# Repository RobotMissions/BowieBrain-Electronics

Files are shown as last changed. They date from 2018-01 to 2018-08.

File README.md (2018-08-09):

# Bowie Brain Board v1.1

Robot Missions logo, a green leaf on a white diamond situated within a purple circle

Bowie Brain Board is the electronics for the [Robot Missions](http://robotmissions.org) introductory robot platform, _Bowie_.

### More information about our robot platform at the [Robot Missions Website ➞](http://robotmissions.org)

The Robot Missions Bowie Brain Board has ports for 6 servos, connections for 4 DC motors (2 controlled independently), can measure the current draw from the servos or DC motors, and has several connections for extendable modules. Microcontroller uses a [Teensy 3.6](https://www.pjrc.com/store/teensy36.html) for full functionality including data logging, or a [Teensy 3.2](https://www.pjrc.com/store/teensy32.html).

Firmware can be found here: [Bowie Library](https://github.com/RobotMissions/BowieLib) and [Bowie Shoreline](https://github.com/RobotMissions/BowieShoreline).

This board was designed in gEDA. You can edit it in [pcb-rnd](http://repo.hu/projects/pcb-rnd/).

## Pinouts

There are several ways you can extend the functionality of your Bowie robot. Here are the labeled connector ports with the according pins.

> **Note:** TX_n_ denotes data out from the brain's microcontroller, and RX_n_ is data in to it.

Labeled connector pinouts

## Schematics

For all pin usage, [see this spreadsheet](https://docs.google.com/spreadsheets/d/1hbOPDjGGXycjbXXOjvf-UFxm08XbPSapu2aIzFMsICY/edit?usp=sharing). _Note: This board was designed without a schematic._

## Board Setups

### Teensy 3.6

The setup for Teensy 3.6 uses the full functionality of the brain board. Solder all of the headers on to the teensy, except for the column in the middle. Make sure the male and female pins in the middle rows line up.

Teensy 3.6 installed in the Robot Missions Brain Board v1.0

### Teensy 3.2

The setup for Teensy 3.2 is a bit different. To get access to all of the servo pins and more of the GPIO, you have to solder a ribbon header out.

Teensy 3.2 installed in the Robot Missions Brain Board v1.0

Following the above image:

| Wire colour in image  |  Teensy 3.2 Pin  |  Bottom Row Header Pin
| :---: | :---: | :---:
| Black | 32 | 24
| White | 31 | 23
| Grey | 30 | 22
| Purple | 29 | 21
| Blue | 28 | 20
| Green | 27 | 19
| Yellow | 26 | 18
| Orange | 25 | 17
| Red | 24 | 16

## Bill of Materials

| Refdes | Description | Source |
| --- | --- | --- |
| N/A | Bowie Brain Board | [Robot Missions](mailto:hello@robotmissions.org) |
| U1 | Microcontroller Teensy 3.6 or Teensy 3.2 | PJRC: [3.6](https://www.pjrc.com/store/teensy36.html), [3.2](https://www.pjrc.com/store/teensy32.html) |
| U2 | Xbee Series 3 with whip antenna | Digikey 602-1560-ND |
| U2 | Xbee headers | Digikey S5751-10-ND |
| U3 | Motor driver TB6612FNG | [A2D Electronics](https://a2delectronics.ca/shop/modules/tb6612fng-motor-driver/) |
| U4 | 3.3V 1A regulator | [Pololu](https://www.pololu.com/product/2830) — Alternate _(less current)_: Digikey 497-7246-1-ND |
| U5, U6 | Current sensor | [Pololu](https://www.pololu.com/product/2453) |
| R1, R2, R3, R4, R5 | 330 Resistors for Xbee LEDs | Digikey 330QBK-ND |
| R6, R7 | 4.7k Pull-up resistors for I2C | Digikey 4.7KQBK-ND |
| R8 | 10K Voltage divider resistor for battery monitor | Digikey 10KQBK-ND |
| R9 | 20K Voltage divider resistor for battery monitor | Digikey 20KQBK-ND |
| R10 | 330 Resistor for speaker | Digikey 330QBK-ND |
| R11 | 2.0K Resistor for speaker | Digikey 2.0KQBK-ND |
| D1, D3 | 5mm Red LED | Digikey C503B-RCN-CX0Y0AA1-ND |
| D2, D4 | 5mm Green LED | Digikey C503B-GAN-CC0D0891-ND |
| D5 | 10mm LED | Digikey VAOL-10GDE4-ND |
| D6 | 1N4001 Diode | Digikey 1N4001-TPMSCT-ND |
| LS | Speaker | Digikey 445-2525-1-ND |
| Q1 | PN2222A Transistor | Digikey PN2222AD26ZCT-ND |
| PWR IN | Barrier block | Digikey A98474-ND |
| J2 | _Optional_ Power supply connection using JST-SM 6 pin | [Adafruit](https://www.adafruit.com/product/1665) |
| J3 | Screw terminals | Digikey A98079-ND |
| J4, J5, J6, J7 | Motor connections using JST-SM | Digikey 1528-1596-ND | 
| N/A | Spade connectors for barrier block | Digikey A0989CT-ND & A100665CT-ND |
| N/A | Coincell holder | Digikey BS-7-ND |
| N/A | 4x M3 8mm mounting screws | Home Hardware |
| N/A | Servo extension cables | [Hobbyking](https://hobbyking.com/en_us/twisted-30cm-servo-lead-extention-jr-22awg-5pcs-set.html) |
| N/A | Headers F | [A2D Electronics](https://a2delectronics.ca/shop/wires-and-connectors/5pcs-40pin-2-54mm-female-headers/) |
| N/A | Headers M | [A2D Electronics](https://a2delectronics.ca/shop/wires-and-connectors/5pcs-40pin-2-54mm-male-headers/) |
| N/A | Micro SD Card | Canada Computers | 
| N/A | 3V Coincell CR2023 | Dollarama |

## License

This board is released under the [CERN Open Hardware License v1.2](https://www.ohwr.org/projects/cernohl/wiki).

## Bug Reports / Feature Requests

Found a bug? Looking for a feature? Let us know by opening an Issue report. Further questions can be posted to our [forum](http://forum.robotmissions.org).

---

🤖✌️🌎

**Robot Missions - Helping the planet with robots**

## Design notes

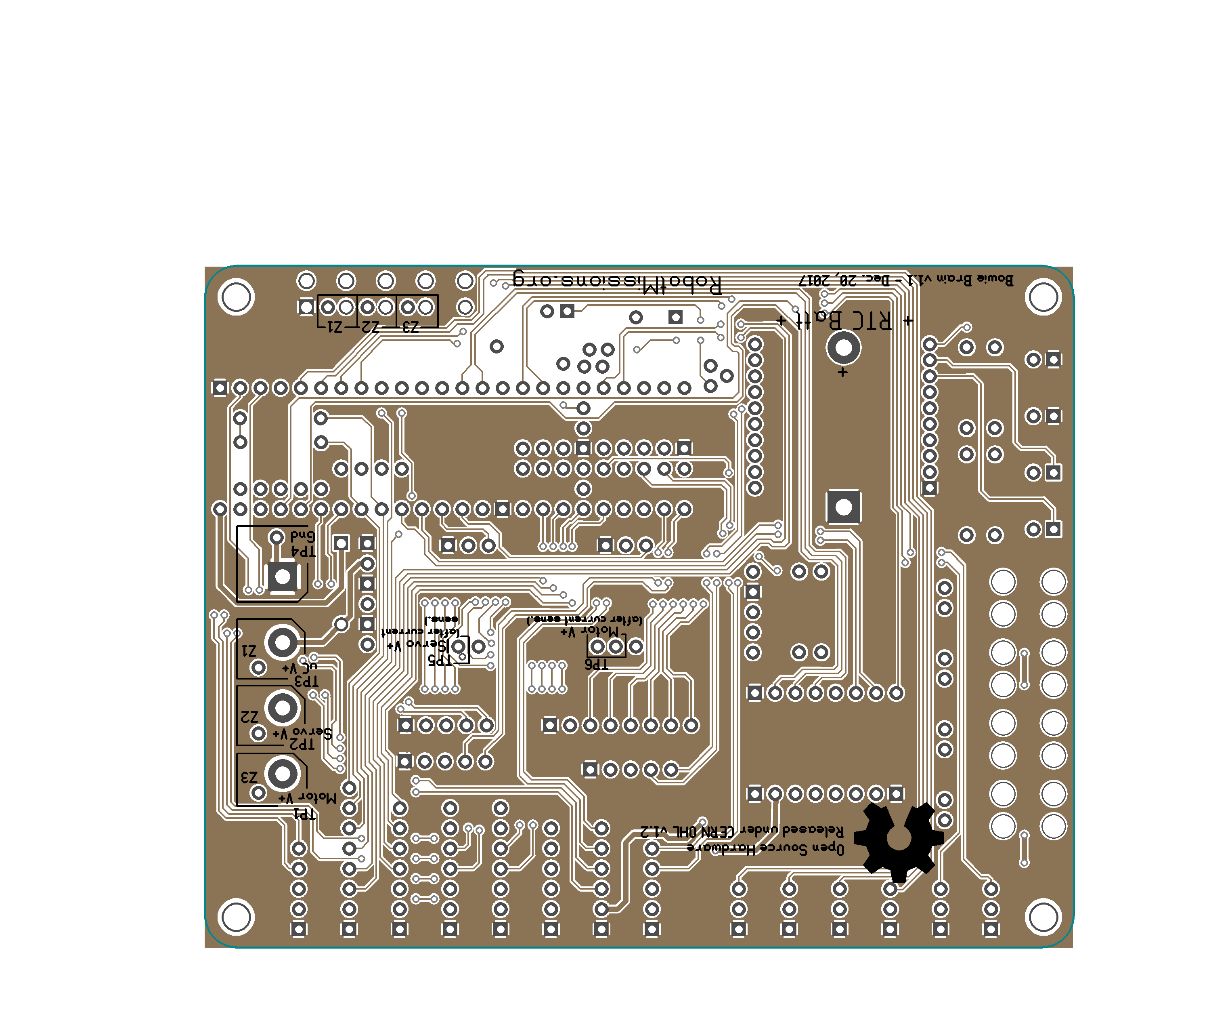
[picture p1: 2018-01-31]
robotmissions_t3.6_brain_bottom.png

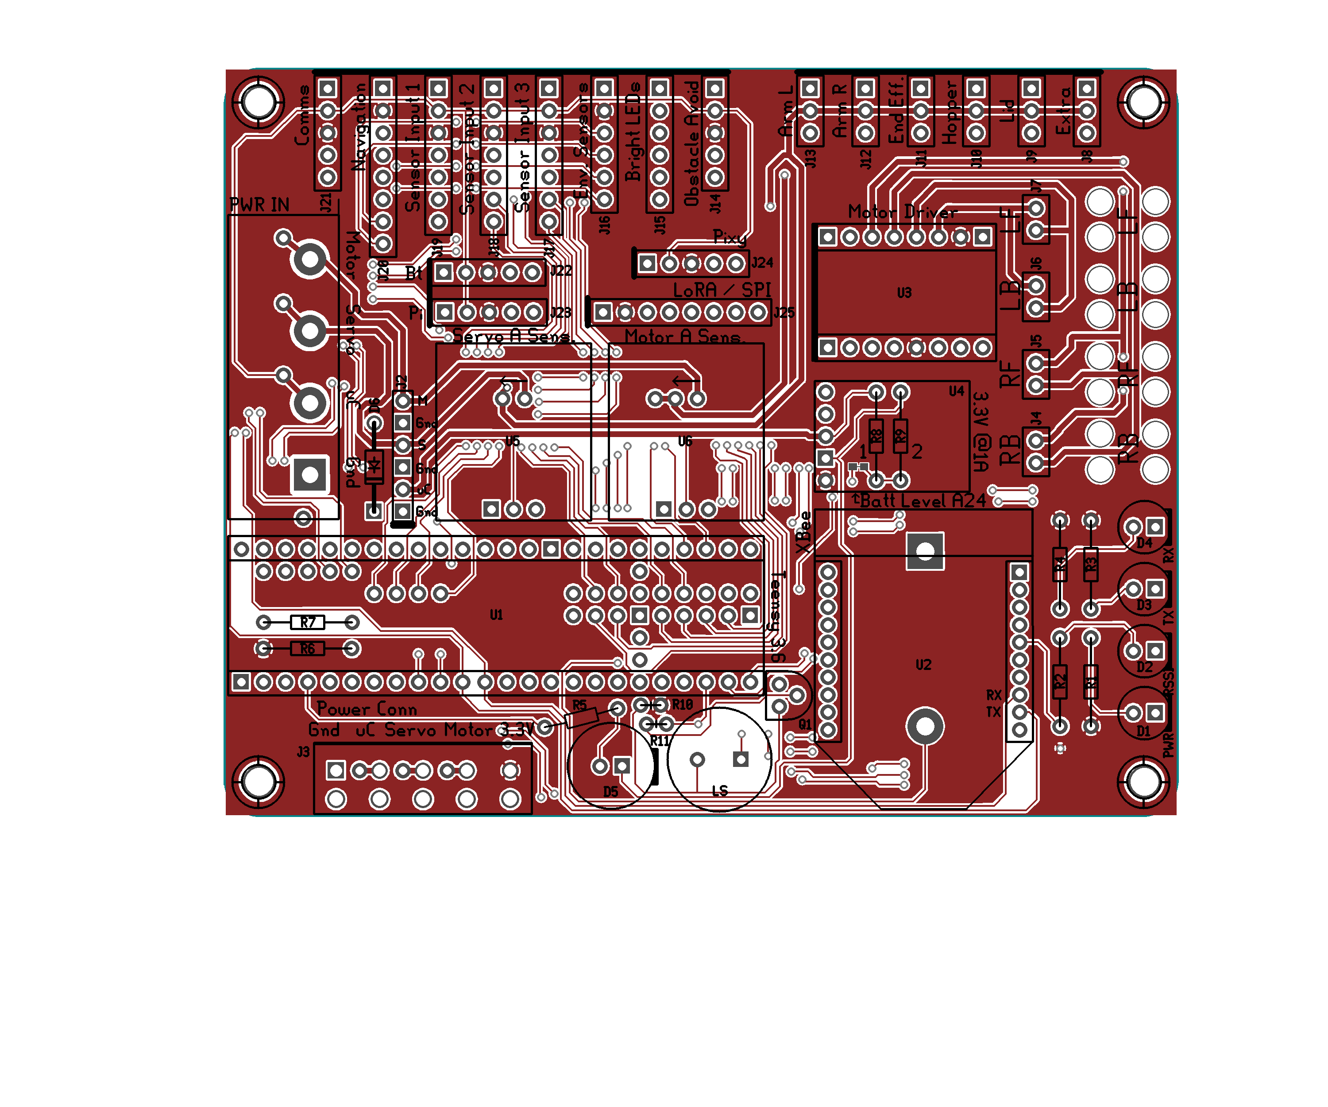
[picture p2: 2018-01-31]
robotmissions_t3.6_brain_top.png

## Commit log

2018-01-31 Hello Bowie Brain
    [robotmissions_t3.6_brain.bottom.gbr, robotmissions_t3.6_brain.bottommask.gbr, robotmissions_t3.6_brain.bottomsilk.gbr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]
2018-02-28 Pushing update to update readme image that had bright leds header power pin improperly labeled
2018-05-11 Updated 10mm LED
2018-08-09 Update to part num for spade connectors
